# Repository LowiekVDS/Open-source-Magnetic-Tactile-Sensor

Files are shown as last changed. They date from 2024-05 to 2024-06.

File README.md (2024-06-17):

### TL;DR

[Paper](https://arxiv.org/abs/2405.18582), also see [this repo](https://github.com/LowiekVDS/masters-thesis) for expanded design.

# Open-source Magnetic Tactile Sensing

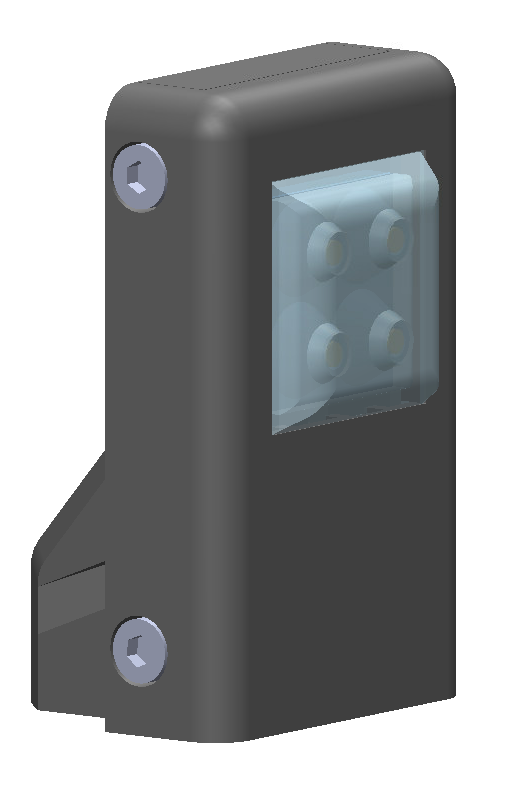
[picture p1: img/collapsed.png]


This repo contains the design files for a magnetic tactile fingertip presented at the [ViTac workshop](https://shanluo.github.io/ViTacWorkshops/) at ICRA2024, you can read the paper [here](https://arxiv.org/abs/2405.18582).
The fingertip has four taxels in a 2-by-2 grid. We developed a calibration method to be used with a robotic arm with integrated F/T sensor. In the paper, the fingertip is mounted to (a gripper the arm and pushed against an external probe to collect calibration data. It is crucial that the mounting of the fingertip to the robot is rigid. We have noticed that this is not sufficiently the case when mounting the fingertip to a Robotiq 2F-85 gripper. A Schunk EGK-40 gave better results. 

This work was expanded upon by designing a 4-by-8 grid as well, together with a more reliable calibration method where the sensor is mounted to the table, see [this repo](https://github.com/LowiekVDS/masters-thesis).

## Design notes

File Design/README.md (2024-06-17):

## Silicone molding

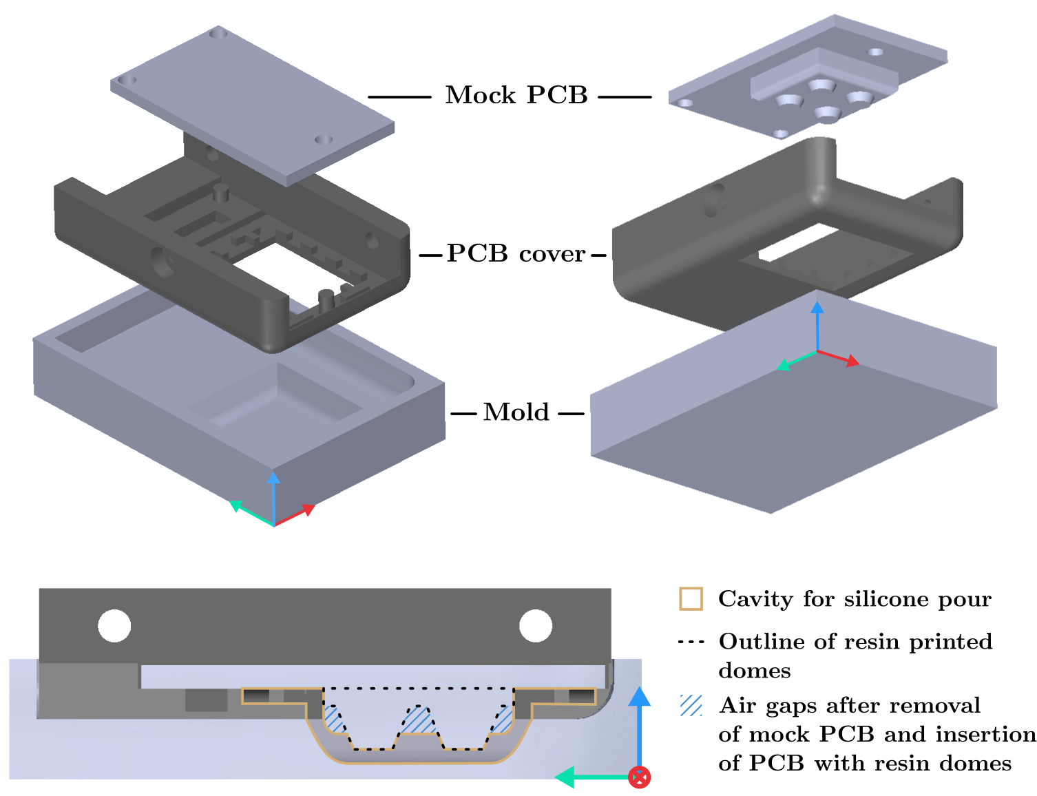
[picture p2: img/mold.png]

<BR CLEAR="all">

## Assembly

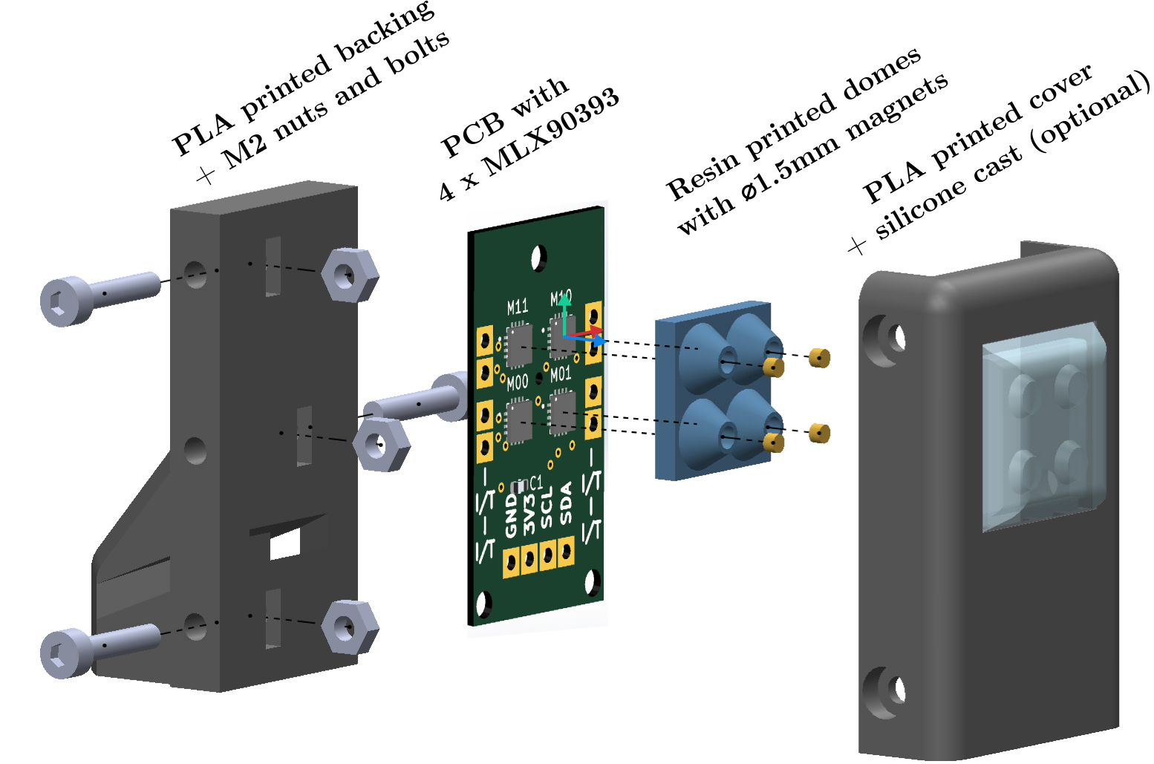
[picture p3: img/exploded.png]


## Probe assembly

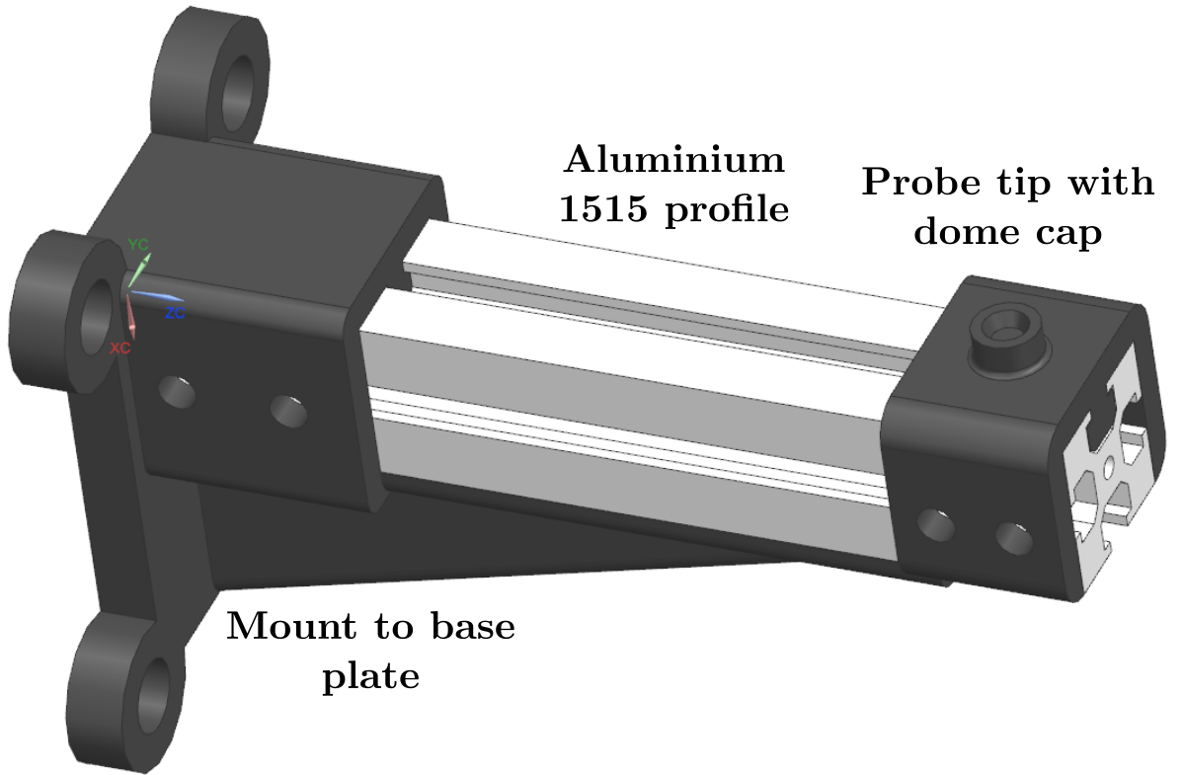
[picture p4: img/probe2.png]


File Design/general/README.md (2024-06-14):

The Robotiq adapter allows you to mount [Robotiq 2F-85 and -140](https://robotiq.com/products/2f85-140-adaptive-robot-gripper) fingertips to [Schunk EGU](https://schunk.com/dk/en/gripping-systems/parallel-gripper/egu/c/PGR_6556)/[EGK](https://schunk.com/ro/en/gripping-systems/parallel-gripper/egk/c/PGR_6557) grippers.

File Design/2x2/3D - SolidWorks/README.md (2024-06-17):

Use pcb_cover_thick during calibration and if you don't require a continuous silicone pad covering the taxels. Use pcb_cover for casting silicone onto.

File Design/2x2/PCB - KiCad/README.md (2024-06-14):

The KiCad component schematics and footprints are in the `lib` folder, make sure to add them in KiCad (Preferences > Manage Symbol Libraries && Preferences > Manage Footprint Libraries).

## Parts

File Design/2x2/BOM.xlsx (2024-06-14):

Electrical (PCB)
Designator | Part | Example link
M00, M01, M10, M11 | MLX90393SLW-ABA-011-RE | https://www.digikey.be/nl/products/detail/melexis-technologies-nv/MLX90393SLW-ABA-011-RE/5031683
C1 | 100nF 0603 capacitor | https://www.digikey.be/nl/products/detail/kyocera-avx/06035C104JAT2A-62/11258798
Mechanical
Item | Part | Example link
Silicone | Siliconen Additie Kleurloos 50 (hard) | https://www.siliconesandmore.com/nl/siliconen-additie-kleurloos-50-hard.html?id=105361103&_gl=1*7twajh*_up*MQ..
Silicone (soft alternative) | Siliconen Additie Kleurloos 5 | https://www.siliconesandmore.com/nl/siliconen-additie-kleurloos-5.html?id=102348485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
Magnets ø1.5mm | DZ-001.5-001-G52 | https://www.neomagnete.de/en/disc-magnet-1-5x1mm-neodym-n52-gilded
Aluminium 1515 profile |  | https://www.123-3d.nl/123-3D-Aluminium-profiel-1515-lengte-1-m-123-3D-huismerk-i1470-t14579.html
3D printed parts |  | https://jlc3dp.com/3d-printing-quote

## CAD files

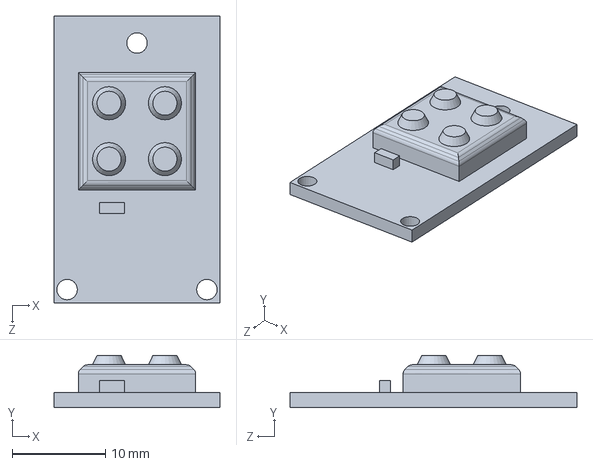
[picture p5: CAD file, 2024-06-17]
Design/2x2/3D - SolidWorks/mock_pcb.SLDPRT
17.8 x 5.60 x 30.8 mm

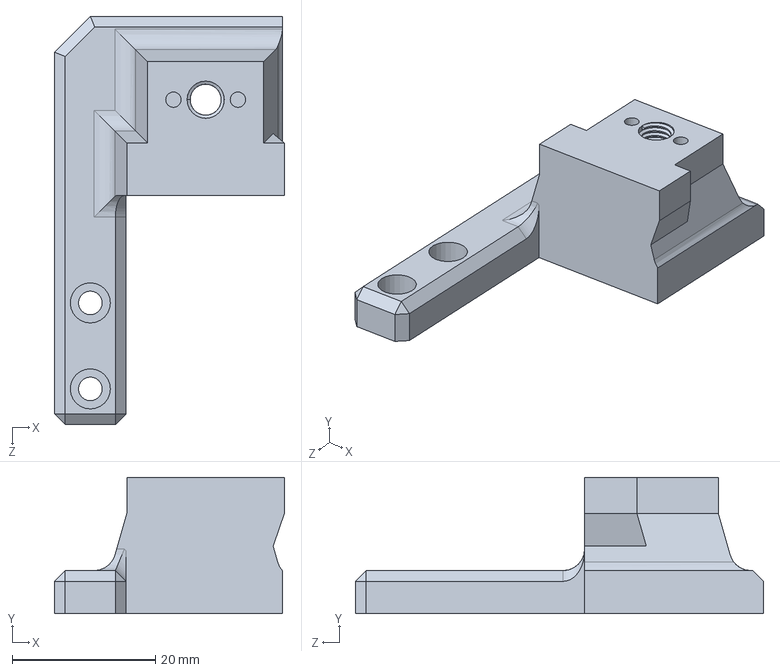
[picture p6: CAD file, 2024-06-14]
Design/general/robotiq_adapter.sldprt
32.1 x 19.0 x 57.0 mm

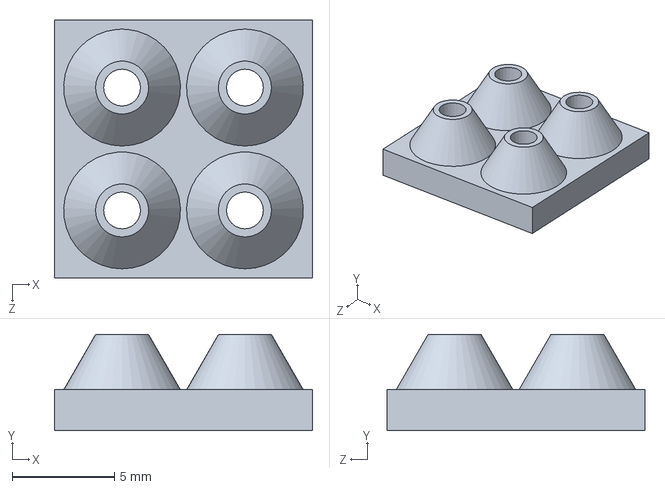
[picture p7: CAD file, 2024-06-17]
Design/2x2/3D - SolidWorks/2x2_domes.SLDPRT
12.6 x 4.70 x 12.6 mm

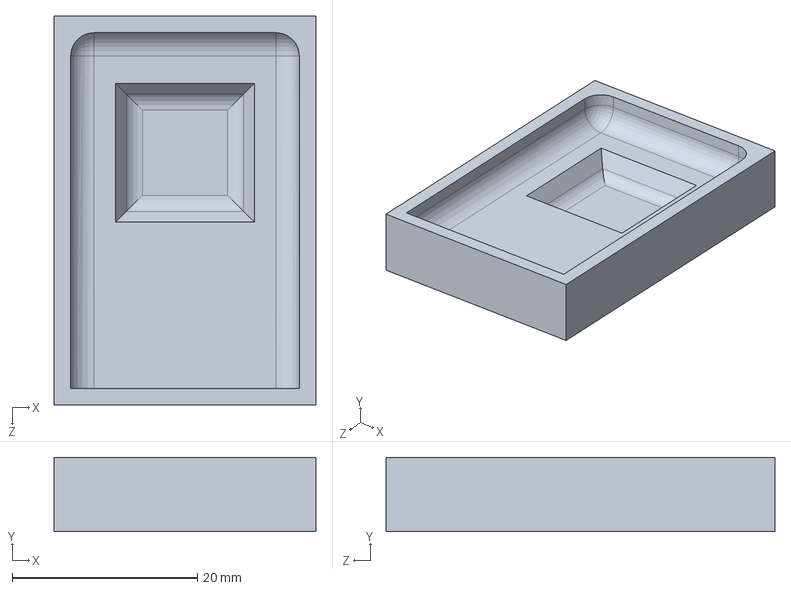
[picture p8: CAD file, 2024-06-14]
Design/2x2/3D - SolidWorks/mold.SLDPRT
28.3 x 8.00 x 42.0 mm

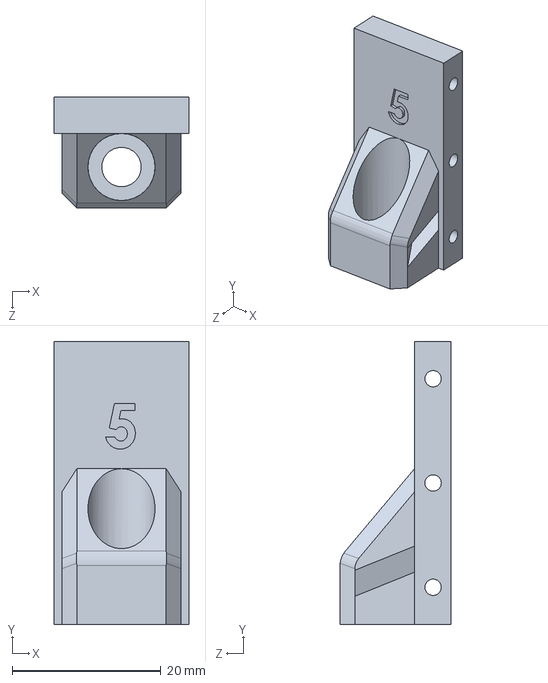
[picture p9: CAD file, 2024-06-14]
Design/2x2/3D - SolidWorks/backing.SLDPRT
18.1 x 38.0 x 14.9 mm

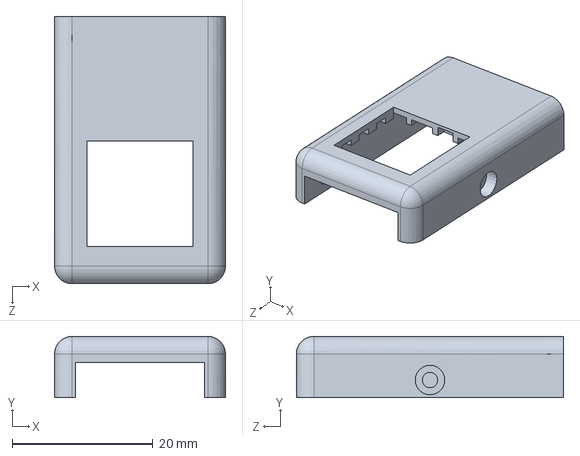
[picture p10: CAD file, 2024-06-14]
Design/2x2/3D - SolidWorks/pcb_cover.SLDPRT
24.3 x 8.70 x 38.0 mm

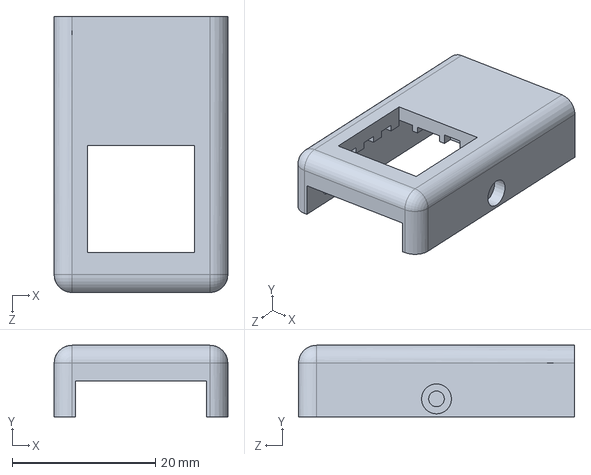
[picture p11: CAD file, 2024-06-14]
Design/2x2/3D - SolidWorks/pcb_cover_thick.SLDPRT
24.3 x 10.0 x 38.6 mm

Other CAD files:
Design/2x2/3D - SolidWorks/2x2_domes.STL
Design/2x2/3D - SolidWorks/backing.STL
Design/2x2/3D - SolidWorks/mock_pcb.STL
Design/2x2/3D - SolidWorks/mold.STL
Design/2x2/3D - SolidWorks/pcb_cover.STL
Design/2x2/3D - SolidWorks/pcb_cover_thick.STL
Design/general/robotiq_adapter.stl

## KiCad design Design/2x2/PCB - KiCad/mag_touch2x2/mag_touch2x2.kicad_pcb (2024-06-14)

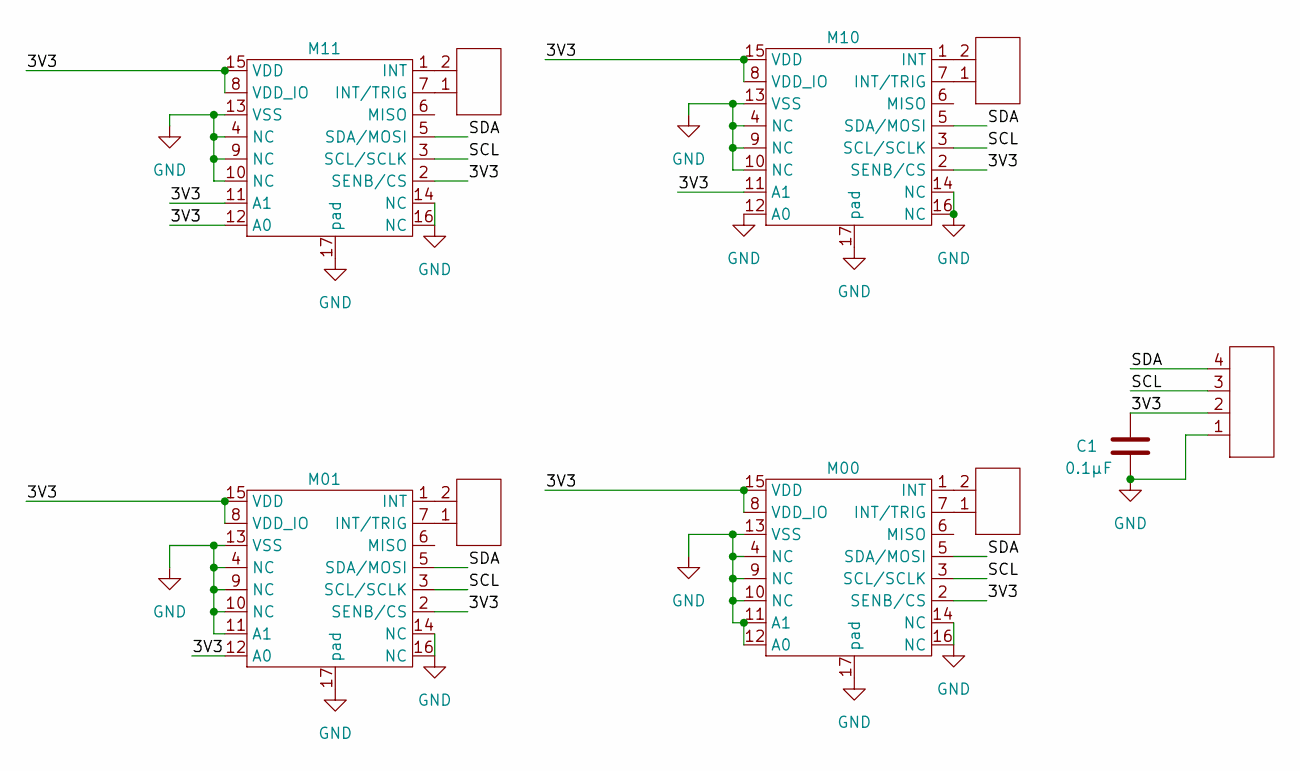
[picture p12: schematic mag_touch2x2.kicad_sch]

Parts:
C1: 0.1µF; C_0603_1608Metric
I1: 2POS_INTERFACE; 4POS_INTERFACE
I2, I3, I4, I5: 2POS_INTERFACE
M00, M01, M10, M11: QFN50P300X300X100-17N

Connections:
/3V3: C1.1, I1.2, M00.2 (SENB/CS), M00.8 (VDD_IO), M00.15 (VDD), M01.2 (SENB/CS), M01.8 (VDD_IO), M01.12 (A0), M01.15 (VDD), M10.2 (SENB/CS), M10.8 (VDD_IO), M10.11 (A1), M10.15 (VDD), M11.2 (SENB/CS), M11.8 (VDD_IO), M11.11 (A1), M11.12 (A0), M11.15 (VDD)
/SCL: I1.3, M00.3 (SCL/SCLK), M01.3 (SCL/SCLK), M10.3 (SCL/SCLK), M11.3 (SCL/SCLK)
/SDA: I1.4, M00.5 (SDA/MOSI), M01.5 (SDA/MOSI), M10.5 (SDA/MOSI), M11.5 (SDA/MOSI)
GND: C1.2, I1.1, M00.4 (NC), M00.9 (NC), M00.10 (NC), M00.11 (A1), M00.12 (A0), M00.13 (VSS), M00.14 (NC), M00.16 (NC), M00.17 (pad), M01.4 (NC), M01.9 (NC), M01.10 (NC), M01.11 (A1), M01.13 (VSS), M01.14 (NC), M01.16 (NC), M01.17 (pad), M10.4 (NC), M10.9 (NC), M10.10 (NC), M10.12 (A0), M10.13 (VSS), M10.14 (NC), M10.16 (NC), M10.17 (pad), M11.4 (NC), M11.9 (NC), M11.10 (NC), M11.13 (VSS), M11.14 (NC), M11.16 (NC), M11.17 (pad)
unnamed: I5.2, M00.1 (INT)
unnamed: I5.1, M00.7 (INT/TRIG)
unnamed: I4.2, M01.1 (INT)
unnamed: I4.1, M01.7 (INT/TRIG)
unnamed: I2.2, M10.1 (INT)
unnamed: I2.1, M10.7 (INT/TRIG)
unnamed: I3.2, M11.1 (INT)
unnamed: I3.1, M11.7 (INT/TRIG)

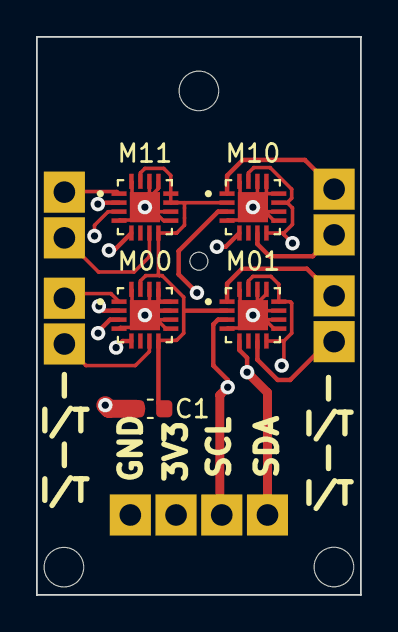
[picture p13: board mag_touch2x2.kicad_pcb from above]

Board: 4 copper layers, 18.0 x 31.0 mm, 10 parts (0 on the bottom side), 12 nets.

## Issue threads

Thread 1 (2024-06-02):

Problems with the hardware system

Newhandsomeman, 2024-06-02:
Hello, I know your work at the ICRA conference.
How is the data collection of MLX sensor completed ?
Excuse me, circuit board design and model files can be open source ?

LowiekVDS, 2024-06-03:
Hello, thanks for your interest! This workshop paper has been written as a part of my master dissertation, which will be submitted on the fifth of June. In this dissertation all resources (CAD, electrical drawings, code ...) will be released in a different repository. So I'll post that link here in a few days!

LowiekVDS, 2024-06-06:
Here you go !

https://github.com/LowiekVDS/masters-thesis

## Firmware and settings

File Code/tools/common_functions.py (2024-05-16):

import pandas as pd
import os
import numpy as np

def prepare_data_for_fitting(name, ARRAY_SIZE=4, SENSOR_LAG = 25, faulty=True):
    
    print(f"Preparing data for fitting: {name}")
    columns = [f'X{i}' for i in range(ARRAY_SIZE)] + [f'Y{i}' for i in range(ARRAY_SIZE)] + [f'Z{i}' for i in range(ARRAY_SIZE)]
    
    # Read in the data
    TFdata = read_csv_file(f"../data/raw/TF/{name}.csv") 
    sensordata = read_csv_file(f'../data/raw/sensor/{name}.csv')
    
    # Take rolling mean
    TFdata['F_x'] = TFdata['F_x'].rolling(window=100).mean()
    TFdata['F_y'] = TFdata['F_y'].rolling(window=100).mean()
    TFdata['F_z'] = TFdata['F_z'].rolling(window=100).mean()

    # Time sync
    data = time_sync_data(sensordata, TFdata, SENSOR_LAG / 1000)
    
    # Remove rows containing NaN values
    data = data.dropna()
    
    # Offset and scale
    data = offset_data(data, columns, 100)
    
    # Remove other columns
    data = data.drop(columns=['t_robot', 'R_x', 'R_y', 'R_z'])

    return data

def unwrap_data(data, columns, threshold=1000):
    
    for col in columns:
        
        np_data = data[col].to_numpy()

        diff = np.diff(np_data)
                
        wrap_points = np.where(np.abs(diff) > threshold)[0]
                
        for point in wrap_points:
            np_data[point+1:] -= diff[point]

        data[col] = np_data

    return data

def read_csv_file(path):
    """
    Reads a CSV file from the specified path and returns the data as a pandas DataFrame.
    
    Parameters:
        path (str): The path to the CSV file.
        
    Returns:
        pandas.DataFrame: The data read from the CSV file.
    """
    
    data = pd.read_csv(os.path.join(os.getcwd(), path))
    
    nr_of_columns = len(data.columns)
    
    # Remove units
    for col in data.columns:
        data[col .split(' ')[0]] = data[col]
    
    # Remove old columns
    data = data.iloc[:, nr_of_columns:]    
    
    return data
    
def read_csv_files(paths):
    """
    Reads all CSV files from the specified path and returns the data as a pandas DataFrame.
    
    Parameters:
        paths (list): list of paths
        
    Returns:
        pandas.DataFrame: The data read from the CSV files.
    """
    
    data = pd.DataFrame()
    
    for p in paths:
        data = pd.concat([data, read_csv_file(p)], ignore_index=True)
    
    return data    

def time_sync_data(df1, df2, df1_lag):

    df1['t_wall'] -= df1_lag
    
    df1_is_first = df1['t_wall'][0] < df2['t_wall'][0]
    sensor_is_last = df1['t_wall'][len(df1)-1] > df2['t_wall'][len(df2)-1]

    if df1_is_first:
        start = df2['t_wall'][0]
    else:
        start = df1['t_wall'][0]
    
    if sensor_is_last:
        end = df1['t_wall'][len(df1)-1]
    else:
        end = df2['t_wall'][len(df2)-1]
    
    # Clip data to start at the same time and also to end at the same time
    df2 = df2[df2['t_wall'] >= start]
    df1 = df1[df1['t_wall'] >= start]
    df2 = df2[df2['t_wall'] <= end]
    df1 = df1[df1['t_wall'] <= end]

    combined = pd.concat([df1, df2], ignore_index=True, sort=False).sort_values(by=['t_wall'])

    combined.set_index('t_wall')
    combined = combined.apply(lambda x: x.interpolate(method='linear')).reset_index()
    
    return combined

def offset_data(data, columns, window=100, startup=100):

    for col in columns:
        data[col] -= np.mean(data[col][startup:startup+window])
        data[col] /= 1000
        
    return data

def normalize_center_data(data, columns):
    """
    Normalizes the data in the specified columns.
    
    Parameters:
        data (pandas.DataFrame): The data to be normalized.
        columns (list): The columns to be normalized.
        
    Returns:
        pandas.DataFrame: The normalized data.
    """
    
    for col in columns:
        data[col] = data[col] / (data[col].max() - data[col].min())
        data[col] = (data[col] - data[col].mean())
        
    return data

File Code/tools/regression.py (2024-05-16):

import numpy as np
import os
import dill
from sklearn.linear_model import LinearRegression, Ridge, ARDRegression
from sklearn.metrics import mean_squared_error
from sklearn.model_selection import train_test_split
from sklearn.compose import ColumnTransformer, make_column_transformer
from sklearn.pipeline import make_pipeline, make_union
from sklearn.preprocessing import PolynomialFeatures
from sklearn import set_config
from sklearn.multioutput import MultiOutputRegressor, RegressorChain
from sklearn.compose import TransformedTargetRegressor

def save_taxel_models(taxel_models, subdir, name):
    
    while '/' in name:
        subdir = os.path.join(subdir, name.split('/')[0])
        name = name.split('/')[-1]
        
    save_path = os.path.join(os.getcwd(), '..', 'models', subdir)

    if not os.path.exists(save_path):
        os.makedirs(save_path)
        
    with open(os.path.join(save_path, name), 'wb') as f:
        dill.dump(taxel_models, f)

def create_regression_pipeline_and_fit(X, Y, debug = True, preserve_time=False, alpha=1, degree=3):
  
  if preserve_time:
    split = int(len(X) * 0.99)
    X_train = X[:split]
    X_test = X[split:]
    y_train = Y[:split]
    y_test = Y[split:]
  else:
    X_train, X_test, y_train, y_test = train_test_split(X, Y, test_size=0.2, shuffle=True)

  pipeline = make_pipeline(
    PolynomialFeatures(degree=degree, include_bias=True), 
    LinearRegression()
  )
  
  pipeline.fit(X_train, y_train)

  if debug:
    
    print("Score: ", pipeline.score(X_test, y_test))
    print("MSE: ", mean_squared_error(y_test, pipeline.predict(X_test)))
  
  return pipeline

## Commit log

2024-06-14 large update
    [BOM.xlsx, backing.SLDPRT, backing.STL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]
2024-06-17 added cad files
    [2x2_domes.SLDPRT, 2x2_domes.STL, mock_pcb.SLDPRT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]
